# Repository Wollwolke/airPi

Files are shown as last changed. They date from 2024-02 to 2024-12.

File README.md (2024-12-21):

# airPi

Software + schematics for controlling ebm-papst fans with a Pi Pico.  
Inspired by [svenjust/room-ventilation-system](https://github.com/svenjust/room-ventilation-system).

## Software

The project is built using PlatformIO and the [Arduino-Pico core](https://github.com/earlephilhower/arduino-pico).

Configuration is done using the [`configuration.hpp`](code/include/configuration.hpp) file.

## Hardware

> ⚠ The 4-pin molex connectors are vertically mirrored.  
> The fans' plugs must be re-pinned when using the current schematics!

Schematics can be found in the [schematics](schematics/) subfolder.  
Datasheets used in this project are in the private submodule [datasheets](https://github.com/Wollwolke/airPi_datasheets/).

### Pico Pinout

| Function | Pin | GPIO |
| --- | --- | ---- |
| SDA | 6 | GP4  |
| SCL | 7 | GP5  |
| Mode Switch 1 | 16  | GP12 |
| Mode Switch 2 | 15  | GP11 |
| Mode Switch 3 | 14  | GP10 |
| Button | 20  | GP15 |
| Tacho 1 | 21  | GP16 |
| Tacho 2 | 22  | GP17 |
| PWM 1 | 25  | GP19 |
| PWM 2 | 27  | GP21 |
| Trimmer | 31  | GP26 |
| Temp Sensor | 32  | GP27 |

### Components

- Controller
  - 2x BL 1X20G8 2,54 20pol. Buchsenleiste ✔
- Display
  - BL 1X20W8 2,54 20pol. Buchsenl., gewinkelt ✔
- Optokoppler: 2x SFH 617A-3 VIS ✔
- Stecker
  - 2x MOLEX 39300040 Molex, Stiftleiste - Mini-Fit Jr ✔
  - 3x MSTBA 3-G 5,08 Leiterplatten-Grundleiste ✔
  - 3x MSTB 3-ST 5,08 Leiterplattenstecker ✔
  - 1x MOLEX 39301020 Molex, Stiftleiste - Mini-Fit Jr ✔
  - 1x MSTBA 4-G 5,08 Leiterplatten-Grundleiste ✔
- Platine
  - LR-DS-79 Lochrasterplatine ✔
- Netzteil
  - AC/DC: IRM-10-12 AC/DC-Wandler ✔
    - **Lochraster checken**
  - Schotkydiode: 1N 5819RL STM ✔
  - LMO78_05-0.5 DC/DC-Wandler ✔
    - TANTAL 10/25 Tantal-Kondensator, Rm 2,5, 10µF/25V ✔
    - TANTAL 22/16 Tantal-Kondensator, Rm 2,5, 22µF/16V ✔
- Passive Komponenten
  - Sicherung (+ Halter)
    - Strom: 1,6A durch Motoren + 0,15A Netzteil
    - ESKA 522.021 Feinsicherung 5x20mm, träge (t), 2,5A ✔
    - ESKA 522.022 Feinsicherung 5x20mm, träge (t), 3,15A ✔
    - 2x PL 120000 Sicherungshalter, 5x20mm, max. 6,3A-500V ✔
    - 2-3x SWC 777098 Temperatursicherung ✔
    - EPC B72220-S 302 Varistor ✔
  - Poti
    - 64P-10K Präzisionspotentiometer ✔
  - Diode aus Schaltplan
    - ZD 11 Zenerdiode ✔
  - K/RES-E3 Sortiment, E3-Widerstände ✔
  - min. 2x KERKO 100N Keramik-Kondensator, 100 nF ✔
- SIK 275 2 Silikonkabel, 0,75 mm² ✔
- KUPFER 0,7MM Kupferlackdraht ✔

## Usage

- Short press
  - In Setup: Switch between Fans
  - Other: Turn on display
- Long press
  - In Setup: Save configuration
  - In Running: Start Setup
- Tripple Press (with 300ms delay)
  - In Running: Enable Serial Setup

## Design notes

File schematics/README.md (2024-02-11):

# Schematics

> ⚠ The 4-pin molex connectors are vertically mirrored.  
> The fans' plugs must be re-pinned when using the current schematics!

## airPi Controller

airPi controller schematic

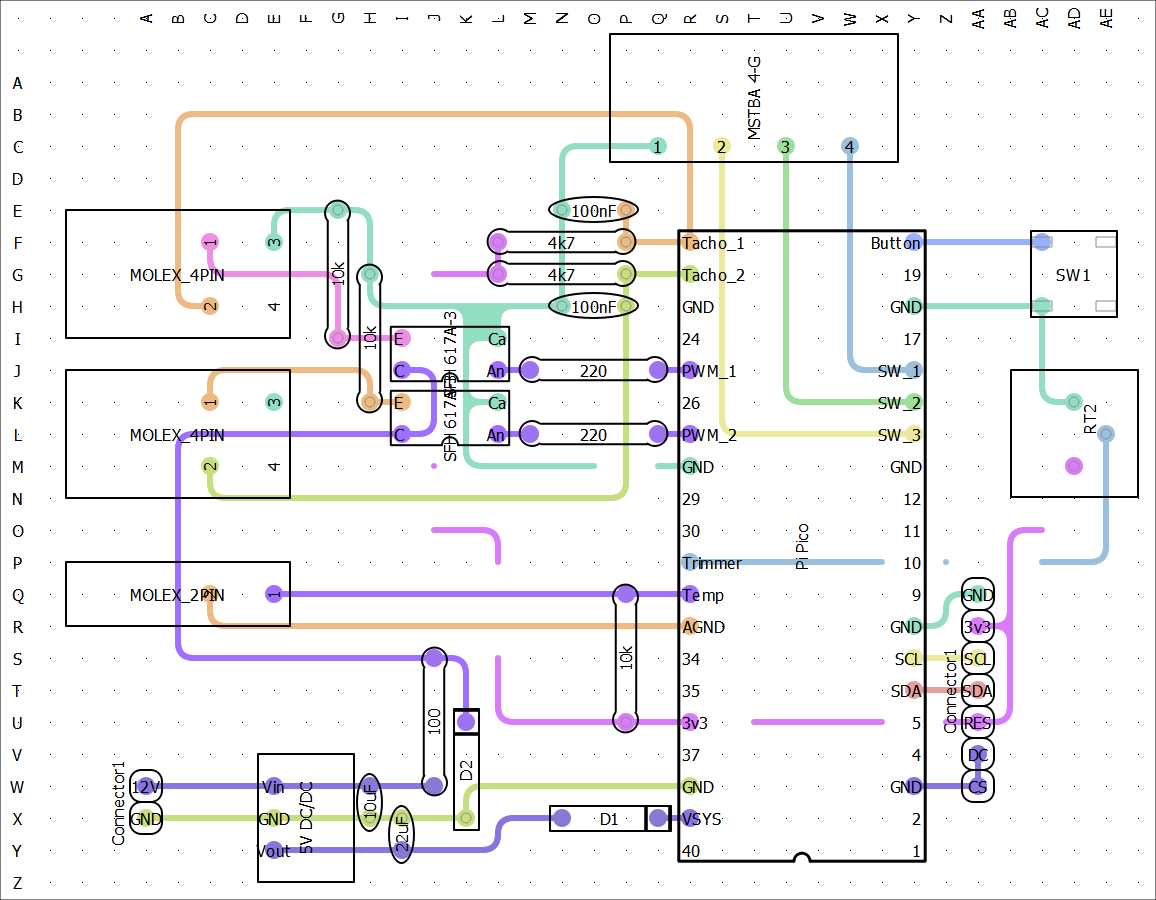
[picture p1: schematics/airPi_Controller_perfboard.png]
airPi controller perfboard


## airPi Power Supply

airPi power supply schematic

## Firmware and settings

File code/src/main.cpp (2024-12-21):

#include <Arduino.h>
#include "configuration.hpp"
#include "configStore.hpp"
#include "tempProbe.hpp"
#include "screen.hpp"
#include "fan.hpp"
#include "debugUtils.hpp"
#include <EasyButton.h>
#include <ResponsiveAnalogRead.h>

using namespace airPi;

void onPressed();
void onLongPress();
void onSequenceMatchedCallback();
void updateScreen();
void runTask();
void readProfile();
void serialSetup();
void checkForErrors();
uint16_t reverseAnalogValue(int16_t analogValue);
uint8_t analogToPercentage(int analogValue);

enum class State : uint8_t
{
    RUNNING,
    SETUP_FAN1,
    SETUP_FAN2,
    SETUP_SERIAL,
    FREEZE,
    ERROR,
};

EasyButton button(Pins::BUTTON, 35, true, true);
ResponsiveAnalogRead analog(Pins::TRIMMER, true);
FanControl fanControl(Pins::FAN_1, Pins::TACHO_1, Pins::FAN_2, Pins::TACHO_2);
TempProbe tempProbe(Pins::TEMP, 10);
Screen screen;
ConfigStore conf;

State state = State::RUNNING;
unsigned long timer = millis();
uint8_t profile_number = 1;
ConfigStore::Profile *profile = conf.getProfile(profile_number);

void setup()
{
    // PSU mode for potentially less noise on ADC
    pinMode(23, OUTPUT);
    digitalWrite(23, HIGH);

    // PWM Output
    analogWriteFreq(490);
    analogWriteResolution(10);

    // 3-way switch
    pinMode(Pins::MODE_1, INPUT_PULLUP);
    pinMode(Pins::MODE_2, INPUT_PULLUP);
    pinMode(Pins::MODE_3, INPUT_PULLUP);
    readProfile();

    // fans
    fanControl.begin();

    screen.begin();
    conf.begin();

    // Button
    button.begin();
    button.onPressed(onPressed);
    button.onPressedFor(2000, onLongPress);
    button.onSequence(3, 500, onSequenceMatchedCallback);

    Serial.setTimeout(SERIAL_TIMEOUT_MS);

    rp2040.wdt_begin(WATCHDOG_TIMEOUT);
    rp2040.wdt_reset();
}

void onPressed()
{
    switch (state)
    {
    case State::SETUP_FAN1:
        state = State::SETUP_FAN2;
        break;
    case State::SETUP_FAN2:
        state = State::SETUP_FAN1;
        break;
    default:
        screen.on();
        timer = millis();
        break;
    }
    D_print("Pressed\n");
}

void onLongPress()
{
    switch (state)
    {
    case State::SETUP_FAN1:
    case State::SETUP_FAN2:
        conf.store();
        timer = millis();
        state = State::RUNNING;
        break;
    case State::RUNNING:
        state = State::SETUP_FAN1;
        screen.on();
        break;
    default:
        screen.on();
        timer = millis();
        break;
    }
    D_print("Long press\n");
}

void onSequenceMatchedCallback()
{
    if (state == State::RUNNING)
    {
        state = State::SETUP_SERIAL;
    }
    D_println("Sequence");
}

void updateScreen()
{
    screen.setTemperature(tempProbe.getTemp());
    screen.setProfile(profile_number);
    screen.setRpm(0, fanControl.getSpeed(0));
    screen.setRpm(1, fanControl.getSpeed(1));
    screen.setSpeed(0, analogToPercentage(profile->fan_1));
    screen.setSpeed(1, analogToPercentage(profile->fan_2));
    switch (state)
    {
    case State::SETUP_FAN1:
        screen.setFanSetup(1);
        break;
    case State::SETUP_FAN2:
        screen.setFanSetup(2);
        break;
    case State::SETUP_SERIAL:
        screen.setFanSetup(3);
        break;
    case State::ERROR:
        break;
    default:
        screen.setFanSetup(0);
        break;
    }
}

void runTask()
{
    switch (state)
    {
    case State::RUNNING:
        // screen timeout
        if (timer + SCREEN_TIMEOUT_S * 1000 < millis())
        {
            screen.off();
        }

        // Control Fans
        fanControl.setPwm(0, profile->fan_1);
        fanControl.setPwm(1, profile->fan_2);

        // Anti-Freeze
        if (tempProbe.getTemp() <= TEMP_ANTIFREEZE_MIN)
        {
            state = State::FREEZE
        }
        break;
    case State::SETUP_FAN1:
    {
        auto analogValue = reverseAnalogValue(analog.getValue());
        profile->fan_1 = analogValue;
        fanControl.setPwm(0, analogValue);
    }
    break;
    case State::SETUP_FAN2:
    {
        auto analogValue = reverseAnalogValue(analog.getValue());
        profile->fan_2 = analogValue;
        fanControl.setPwm(1, analogValue);
    }
    break;
    case State::SETUP_SERIAL:
        serialSetup();
        break;
    case State::FREEZE:
        fanControl.setPwm(0, 0);
        fanControl.setPwm(1, 0);
        if (tempProbe.getTemp() > TEMP_ANTIFREEZE_MAX)
        {
            state = State::RUNNING;
        }
        break;
    case State::ERROR:
        fanControl.setPwm(0, 0);
        fanControl.setPwm(1, 0);
        break;
    default:
        break;
    }
}

void readProfile()
{
    uint8_t old_profile = profile_number;

    if (digitalRead(Pins::MODE_1) == LOW)
    {
        profile_number = 1;
    }
    else if (digitalRead(Pins::MODE_2) == LOW)
    {
        profile_number = 2;
    }
    else if (digitalRead(Pins::MODE_3) == LOW)
    {
        profile_number = 3;
    }
    else
    {
        // missing connection --> profile 1
        profile_number = 1;
    }
    if (profile_number != old_profile)
    {
        profile = conf.getProfile(profile_number);
    }
}

void serialSetup()
{
    static uint8_t fan_number = 0;
    static uint16_t set_value = profile->fan_1;
    String serial_input;
    Serial.printf("Fan %i - Poti: %i RPM: %i\n", fan_number + 1, set_value, fanControl.getSpeed(fan_number));

    rp2040.wdt_begin(SERIAL_TIMEOUT_MS * 5);

    if (Serial.available() > 2)
    {
        serial_input = Serial.readStringUntil('\n');

        // Exit setup
        if (strstr(serial_input.c_str(), Commands::STORE))
        {
            state = State::RUNNING;
            conf.store();
            rp2040.wdt_begin(WATCHDOG_TIMEOUT);
        }
        // Switch Fan
        else if (strstr(serial_input.c_str(), Commands::SWITCH_FAN))
        {
            fan_number ^= 1;
        }
        else
        {
            set_value = atoi(serial_input.c_str());
            set_value = constrain(set_value, 0, 1023);
        }
        fanControl.setPwm(fan_number, set_value);
        if (fan_number == 0)
        {
            profile->fan_1 = set_value;
        }
        else
        {
            profile->fan_2 = set_value;
        }
    }
}

uint16_t reverseAnalogValue(int16_t analogValue)
{
    return 1023 - analogValue;
}

uint8_t analogToPercentage(int analogValue)
{
    return static_cast<uint8_t>(constrain(map(analogValue, 2, 1018, 0, 100), 0, 100));
}

void checkForErrors()
{
    // check Temperature sensor
    if (tempProbe.getTemp() < TEMP_MIN)
    {
        state = State::ERROR;
        screen.showError(Errors::TEMP_OPEN);
    }
    else if (tempProbe.getTemp() > TEMP_MAX)
    {
        state = State::ERROR;
        screen.showError(Errors::TEMP_SHORTED);
    }
    if (State::RUNNING == state && millis() / 1000 > STARTUP_TIME_S)
    {
        if (fanControl.getSpeed(0) <= 0)
        {
            state = State::ERROR;
            char text[26];
            strcpy(text, Errors::FAN_NO_TACHO_SIGNAL);
            text[24] = '1';
            text[25] = '\0';
            screen.showError(text);
        }
        else if (fanControl.getSpeed(1) <= 0)
        {
            state = State::ERROR;
            char text[26];
            strcpy(text, Errors::FAN_NO_TACHO_SIGNAL);
            text[24] = '2';
            text[25] = '\0';
            screen.showError(text);
        }
    }
}

void loop()
{
    rp2040.wdt_reset();
    button.read();
    tempProbe.update();
    analog.update();
    readProfile();
    updateScreen();
    checkForErrors();
    runTask();
}

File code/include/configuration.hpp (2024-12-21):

#pragma once
#include <stdint.h>

#define DEBUG 1

constexpr uint8_t SCREEN_TIMEOUT_S = 120;
constexpr uint8_t STARTUP_TIME_S = 30;
constexpr uint8_t PROFILE_COUNT = 3;

constexpr uint16_t SERIAL_TIMEOUT_MS = 2000;
constexpr uint16_t WATCHDOG_TIMEOUT = 500;

// Antifreeze
constexpr int8_t TEMP_MIN = -40;
constexpr uint8_t TEMP_MAX = 50;
constexpr float TEMP_ANTIFREEZE_MIN = 1.5;
constexpr float TEMP_ANTIFREEZE_MAX = 3;

// Temperature sensor calibration
// Messgeräte
// constexpr float TEMP_A = 1.756973732e-3;
// constexpr float TEMP_B = 1.243720261e-4;
// constexpr float TEMP_C = 5.242421439e-7;

// Pico
constexpr float TEMP_A = 2.044911948e-3;
constexpr float TEMP_B = 0.7596940045e-4;
constexpr float TEMP_C = 7.252226919e-7;
constexpr int TEMP_R = 9860;
// 46 4,82 4,858
// 23.8 12.34 12,370
// -12  61.1   57000

// Pins
namespace Pins
{
    constexpr uint8_t MODE_1 = 12;
    constexpr uint8_t MODE_2 = 11;
    constexpr uint8_t MODE_3 = 10;
    constexpr uint8_t BUTTON = 15;
    constexpr uint8_t TACHO_1 = 16;
    constexpr uint8_t TACHO_2 = 17;
    constexpr uint8_t FAN_1 = 19;
    constexpr uint8_t FAN_2 = 21;
    constexpr uint8_t TRIMMER = 26;
    constexpr uint8_t TEMP = 27;
}

// Errors
namespace Errors
{
    constexpr char TEMP_SHORTED[] = "Temperature sensor shorted";
    constexpr char TEMP_OPEN[] = "Temperature sensor not connected";
    constexpr char FAN_NO_TACHO_SIGNAL[] = "No Tacho Signal for fan ";
}

// Commands
namespace Commands
{
    constexpr char SWITCH_FAN[] = "switch";
    constexpr char STORE[] = "store";
}

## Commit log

2024-02-11 added schematics
    [airPi_Controller.schdoc, airPi_HV.schdoc]
2024-02-11 readme: added link to Arduino-pico
2024-12-21 Enabled error checks, increased startup_time, added usage example
    [configuration.hpp, main.cpp]
